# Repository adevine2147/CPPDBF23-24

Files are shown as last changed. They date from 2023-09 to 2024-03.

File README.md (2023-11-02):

# Latest Week Summary (Week 9):
Week # 9     Date: 10/21/23    -    10/27/23

# Aerodynamics Team
### Due milestones:
### Completed milestones: 
### Cost: $0
### Upcoming milestones: 
### Additional Comments:

# Structures Team
### Due milestones: 
### Completed milestones:
### Cost: $0
### Upcoming milestones:
### Additional Comments:

# Payload Team
### Due milestones: 
### Completed milestones:
### Cost: $0
### Upcoming milestones:
### Additional Comments:

# Systems Team
### Due milestones: Finish first draft for Proposal
### Completed milestones: Finishing first draft by Saturday 28
### Cost: $0
### Upcoming milestones: Received feedback and fix proposal on Monday the day before submission.
### Additional Comments:

# Budget
| Subteam | Total | Spendings (This week) | Remaining |
| --- | --- | --- | --- |
| Aerodynamics Team | 800.0 | 0.0 | 800.0 |
| Structures Team (Wed) | 2358.25 | 0.0 | 2358.25 |
| Structures Team (Fri) | 2414.03 | 0.0 | 2414.03 |
| Payload Team | 1000.0 | 0.0 | 1000.0 |
| Systems Team | 200.0 | 0 | 200.0 |

# CPP DBF 23 - 24

This repository is dedicated to efficiently managing Computer-Aided Design (CAD) files, Gantt charts and general file storage for your project.

## Table of Contents

1. [Getting Started](#getting-started)

- [Prerequisites](#prerequisites)

- [Cloning the Repository](#cloning-the-repository)

2. [Uploading](#uploading)

 - [Pushing Changes to GitHub](#pushing-changes-to-github)

 - [Pulling Updates from GitHub](#pulling-updates-from-github)

## Getting Started

  Here's a flowchart
```mermaid
	flowchart TD
A[Terminal go to repo folder on local]-->B[git pull]
B  -->  C[make changes/upload files]

C  -->D[git add .]

C  -->E[git add your-new-file]

D-->  F

E  -->F[git commit -m 'your-commit-messages']

F  -->G[git push]

```

### Prerequisites

Before you begin using this GitHub repository, please ensure that you have the following:

- A GitHub account: If you don't have one yet, you can [sign up here](https://github.com/join).

- Git installed on your local machine. You can download it from [here](https://git-scm.com/downloads).

### Cloning the Repository

To get started, you'll need to clone the repository to your local machine. Open your terminal or Git Bash and use the following command:

```bash

git  clone  https://github.com/adevine2147/CPPDBF23-24.git
```

## Uploading

1.  **Uploading  Files**:

-  To  upload  files  to  your  repository,  click  the  "Add file"  button,  and  then  select  "Upload files"  from  the  dropdown.

-  Drag  and  drop  your  files  into  the  file  upload  area,  or  click  the  "choose your files"  link  to  browse  and  select  files  from  your  local  machine.

-  You  can  add  multiple  files  at  once.

2.  **Commit  Changes**:

-  After  selecting  your  files,  scroll  down  and  provide  a  brief  description  of  the  changes  you're making in the "Commit changes" section.

- Optionally, you can provide a longer description in the "Extended description" field.

3. **Commit New Files**:

- Click the "Commit changes" button to add your files to the repository.

## Pushing Changes to GitHub

1. **Make Local Changes**:

- Before pushing changes, you need to make changes to the files on your local machine. You can edit, add, or delete files as needed.

2. **Stage Changes**:

- In your terminal or Git client, use the following command to stage your changes:

```bash

git add .

```

-  This  command  stages  all  changes  for  commit.

```bash

git add {filename}

```

-  This  command  stages  specific  files  for  commit.

3.  **Commit  Changes**:

-  Commit  your  changes  with  a  descriptive  message  using  this  command:

```bash

git commit -m "Your commit message here"

```

4.  **Push  Changes  to  GitHub**:

-  To  push  your  local  changes  to  the  GitHub  repository,  use  the  following  command:

```bash

git push

```

## Pulling Updates from GitHub

1.  **Fetch  Remote  Changes**:

-  To  update  your  local  repository  with  changes  from  the  remote  repository (GitHub), use the following command:

```bash

git fetch origin

git pull

```

That's it! You've  successfully  learned  how  to  upload  files,  push  changes,  and  pull  updates  in  GitHub!

Latest Week Summary (Week 2):
this is week 2 test

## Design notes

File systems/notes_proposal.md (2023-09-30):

# AIAA Design/Build/Fly Competition - Top Proposals Analysis

## Common Elements:

- **Clear Objectives**: All three proposals have a clear understanding of the competition's objectives and requirements. They emphasize the importance of meeting specific mission goals and scoring criteria.

- **Structured Approach**: Each proposal follows a structured approach, including sections on executive summaries, team organization, conceptual design, manufacturing plans, and test planning. This organization makes it easier for judges to navigate and evaluate the content.

- **Technical Details**: The proposals provide technical details related to aircraft design, including aerodynamics, propulsion, materials, and structural analysis. They show a strong understanding of engineering principles and how they apply to the competition.

- **Sensitivity Analysis**: Sensitivity analysis is used in all three proposals to optimize the design for mission success. This demonstrates a data-driven approach and an understanding of the interplay between design parameters and mission outcomes.

- **Iterative Design**: The proposals emphasize iterative design and testing, indicating a commitment to refining the aircraft's performance through practical experimentation.

- **Team Organization**: Each team has a well-organized structure with designated roles and responsibilities, including faculty advisors. This demonstrates effective teamwork and leadership.

## What They Are Doing Right:

- **Mission Focus**: All proposals prioritize the most critical mission (in this case, Mission 3) based on sensitivity analysis, demonstrating a strategic approach to scoring maximum points.

- **Mathematical Modeling and Simulations**: They make effective use of mathematical modeling and simulations (e.g., MATLAB, CFD) to inform their design decisions and optimize performance.

- **Detailed Manufacturing Plans**: The proposals outline comprehensive manufacturing plans, specifying materials, fabrication techniques, and quality control measures.

- **Testing Strategy**: Each team has a well-thought-out testing strategy that includes both ground and flight tests. This iterative approach helps identify and address design flaws.

- **Financial Planning**: Budgeting and financial planning are included, showing an awareness of the costs associated with participating in the competition.

## What Judges Are Likely Looking For:

When grading these proposals, judges are likely looking for the following key factors:

- **Innovation**: Judges may be interested in innovative design solutions and unique approaches to solving the competition's challenges.

- **Technical Competence**: They expect a strong grasp of engineering principles, as demonstrated through the technical content of the proposals.

- **Mission Optimization**: The ability to optimize the aircraft design to maximize mission-specific scores is likely to be highly valued.

- **Teamwork and Leadership**: Effective team organization, leadership, and collaboration are essential, as they reflect the team's ability to execute their plan.

- **Practicality**: Judges may assess the feasibility and practicality of the proposed design and manufacturing processes.

- **Data-Driven Decision-Making**: The use of data, simulations, and sensitivity analysis to drive design decisions and achieve mission goals is likely to be positively evaluated.

- **Safety and Reliability**: Ensuring the safety and reliability of the aircraft through thorough testing and quality control measures is crucial.

- **Budget Management**: Judges may consider how well the teams have managed their budgets and secured funding for their project.

**Areas for Improvement (Common Across Proposals):**

1.  **Subcomponent Design Schedule:** The proposals lack detailed schedules for subcomponent design. Providing comprehensive schedules for the design and development of individual components could strengthen all three proposals.
    
2.  **Optimization of Ground Mission Weight and Antenna Length:** The proposals could benefit from more detailed information about the teams' approaches to optimizing ground mission weight and antenna length. Offering specific strategies and calculations related to these parameters could enhance the proposals.

3. Ground Mission: The proposal lacks information about the ground mission, including details about the weight to be loaded onto the aircraft. Providing a comprehensive plan for the ground mission would enhance the proposal.

4. Payload Range: The proposed payload range of 1-20 pounds is considered unrealistic. Consider specifying a more reasonable payload range.

5 Optimization and Trade Studies: The methods used for optimization and trade studies could be explained in more detail to provide greater transparency.

6. Design Consistency: Ensure that the proposal maintains consistency between textual descriptions and graphical representations. For example, clarify whether the wing design is rectangular or tapered, and ensure that the number of fasteners aligns with competition rules.

7. Weight, Drag, and Energy Estimation: Include discussions about weight, drag, and mission energy estimation methods. Provide a breakdown of expected empty weight or a goal empty weight.

8. Wind Tunnel Testing: If wind tunnel testing is part of the plan, ensure it is discussed in the proposal, as it appears as a block in the schedule.

9. Testing Plan Detail: Strengthen the description of the testing plan by providing more comprehensive details.

10. Clarify and Correct Discrepancies: Address discrepancies between textual descriptions and visual representations, such as the wing design and fastener counts.

11. Schedule for Prototype Manufacturing: Include a schedule for the manufacturing of the prototype, as it is a crucial aspect of the project.

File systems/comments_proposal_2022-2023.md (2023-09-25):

**Really good proposal overall.** I would like to have seen something on the ground mission - **how much are you planning on loading it to?** Also, a payload range of **1-20 lb is kinda crazy.** Perhaps a smaller volume allotment that could be loaded to a more realistic range. Great work on manufacturing and testing. Those sections are hard at this point in the process, but critical. If you are not thinking about it now, you risk not getting there by the end.

**Good summary and management review.** I think you would have benefitted from explaining your optimization and trade study methods in more detail. Text says you're using a rectangular wing, but picture shows a tapered wing. Discrepancies like this lead to loss of confidence in your explanation. Rules say **2 fasteners to secure antenna, but picture shows 4. Be sure to correct this for your final design.** No discussion of weight, drag, or mission energy estimation methods. Do you have a breakdown of expected empty weight or goal empty weight? How did you optimize box dimensions? The testing plan description is weak. I think you should have devoted more space to that. "**Strongly encouraged to collaborate**" sentence adds no point value, but not talking about wind tunnel testing after showing that as a block in your schedule does reduce your proposal score. Overall, you have what appears to be a good starting point for a successful airplane.

**Team, Overall, well done.** The report was clear and concise. It was obvious that a lot of effort had been expended. The design is well thought out, and shows all areas were considered. **It is important to include a schedule for the manufacturing of the prototype.** All graphics were easy to follow and attractive. Keep up the good work.

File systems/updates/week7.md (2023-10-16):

summary: Week # 7 Date: 10/07/23 - 10/13/23

# Aerodynamics Team

### Due milestones: 
Trade Studies must be done and start XFLR5 practice

### Completed milestones:
A presentation was shared by Andrew for XFLR5 usage and some airfoils were practiced. Some trade studies needed an extra week.

### Cost: $0
(Description of cost, don’t put it in the same line as above)

### Upcoming milestones:
Ansys aircraft simulation will be given to learn and keep XFLR5 practice.

***Additional Comments:***

# Structures Team
 Wednesday 10/11-2023

### Due milestones:
Practice Laminate Wings

Step 1) Move outside with materials to a shaded area
Step 2) Bring two tables
Step 3) Measure:
Part to Vacuum
Vacuum Bag
Gum tape
Peel Fly
Breathing fabric
Step 4) Cut all materials for part
Step 5) In a vacuum bag cut a hole approx. ¼ inch make a cross (X)

Step 6) Stick the vacuum seal
Step 7) Put breathing fabric and peel fly inside the vacuum bag
Step 8) Wear Large gloves and masks cut out carbon fiber to size
Step 9) Wait for resin

### Completed milestones:
Finished practicing laminate wings
 
### Cost: $32.29
(Description of cost, dont put it in the same line as above)

### Upcoming milestones:

***Additional Comments:***

# Payload Team

### Due milestones:

### Completed milestones:

### Cost: $0
(Description of cost, dont put it in the same line as above)

### Upcoming milestones:

***Additional Comments:***

# Systems Team

### Due milestones: 
Start working on Section 4.0

### Completed milestones: 
Section 4.0 waiting for updates for trade studies but the general format already started

### Cost: $0
(Description of cost, dont put it in the same line as above)

### Upcoming milestones: 
Start Gantt Chart for proposal and presentation

***Additional Comments:***

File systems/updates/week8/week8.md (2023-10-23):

summary: Week # 8     Date: 10/14/23    -    10/20/23

# Aerodynamics Team

### Due milestones: 
 Practice XFLR5 and finish trade studies.
### Completed milestones:
Practice was done for XFLR5 and all trade studies were finished. Friday's meeting worked together in XFLR5 for the model and discussed trade studies.
### Cost: $0
### Upcoming milestones: 
### Additional Comments: N/A

# Structures Team
### Due milestones: Assemble and weigh wing for trade study. Finish first practice of wing laminate.
### Completed milestones: Assemble and weigh wing for trade study and wing laminated.
### Cost: $0
### Upcoming milestones: Make a Plan before Aero Data is given.
### Additional Comments: N/A

# Payload Team
### Due milestones: SolidWorks drawing for payload.
### Completed milestones: The First SolidWorks drawing started and dimension analysis is in progress for each mission. 
### Cost: $0
### Upcoming milestones: Mock fuselage dimension shared, keep working on drawing taking into account updated information.
### Additional Comments: N/A

# Systems Team
### Due milestones: Section 4.0 Framework.
### Completed milestones: The section 4.0 framework was done, and in Section 3.0 we started studying trade studies done by the Aero Team. Section 2.0 was started and the first draft was finished.
### Cost: $0
### Upcoming milestones: Correction needed for different sections of the proposal Sections 1.0, 2.0. With help from CE start working on section 3.0.
### Additional Comments: N/A

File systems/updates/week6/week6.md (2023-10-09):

summary: Week # 6     Date: 09/30/23    -    10/06/23

# Aerodynamics Team
### Due milestones: 
Meeting 10/02/2023 Trade matrix updates and progress check-in.
### Completed milestones: 
Most components finished 80% completed Airfoil NACA estimated: 64-ish.
### Cost: $0
### Upcoming milestones: 
Complete trade matrix and share to the Structures team and start CAD. 
***Additional Comments: ***
Got to contact people who did not make it to the meeting and share updates for the structures team.

# Structures Team (Wed)
### Due milestones: 
Learn the program for structures machines for next week's practice for laser and foam cutting.
### Completed milestones: 
 Had the team gather two airfoils: NACA 0012 & NACA 4412 from the NACA Airfoil Website and convert it into a SVG file to be edited in Inkscape. This allowed it to be compatible with the Hotwire Foam Cutter (HWFC) and allowed for the creation of a hole for the wing spar. 
It was then exported as a .DXF file into Vector Tracer which allowed it to create the basic command for the airfoil. Then finally exported as a tap file which was the file type that the HWFC (via MACH 4) would read in order to correctly cut out the airfoil. 
A dry run was first done in order to correctly verify if the HWFC was functioning correctly. The material used for the cutting was a pink insulation foam with 2 in of thickness in order to cut both airfoil shapes with a 2.5 ft span. This was done at 25 PSI.
### Cost: $109.46 
(total cost = [$49.98 * 2] + Tax) ( For the Styrofoam used)
### Upcoming milestones: 
The Wednesday team will study vacuum bagging techniques, resin safety, and handling safety for laminated materials such as: carbon fiber and fiberglass.
***Additional Comments: N/A***

# Structures Team (Fri)
### Due milestones: 
Members are looking to go through the Innovation Idea Labs training, analysis of wing geometry, and begin trade studies.
### Completed milestones: 
Arrival at the Innovation Idea Labs (IIL) in order to use the Laguna Laser CNC to cut out an 18 in Cord airfoil following the NACA 0012 & 4412 patterns. If there is time, then the team will practice putting Mylar (also known as BoPET) on existing wings in the lab.
### Cost: $85.97 
(2'x4'x1/4" plywood sheets 2BC 1Birch)
### Upcoming milestones: 
Make 12 in versions of both airfoils, due next Friday. Possibly also preparing for cutting 3.16 in balsa wood.
***Additional Comments: N/A***

# Payload Team
### Due milestones: 
Updates on payload bay design drafts.

### Completed milestones:
Team getting familiar with Solidworks and beginning a rough design of the dimensions of the payload bay for Structures/Manufacturing.
### Cost: $0
### Upcoming milestones:
Finish payload bay design by Friday (10/13/2023) with a top, side, and frontal view of payload dimensions. Also begin brainstorming a latching method to access the payload.
***Additional Comments: ***
Structures/Manufacturing and Payload are still waiting on Aero for dimensions of the fuselage.

# Systems Team
### Due milestones: 
Finish sections 1.0, 2.0, and 3.0 for the proposal, and start section 4.0.
### Completed milestones: 
Finish section 1.0 and partial of 3.0 for the proposal

### Cost: $0
### Upcoming milestones: 
Finish the Gantt Chart and start updating with Structures for the manufacturing plan on proposal 4.0, section 3.0, and Section 2.0 from the PM by October 11th
***Additional Comments:***

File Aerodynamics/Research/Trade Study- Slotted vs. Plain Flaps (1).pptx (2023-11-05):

## Plain Flaps vs Slotted Flaps

Brandon Henry

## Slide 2

Background

Slotted flaps are an option for the plane, because this design allows high air pressure to flow through the slot, which adds "energy to the wing's boundary layer, delays airflow separation, and produces less drag"

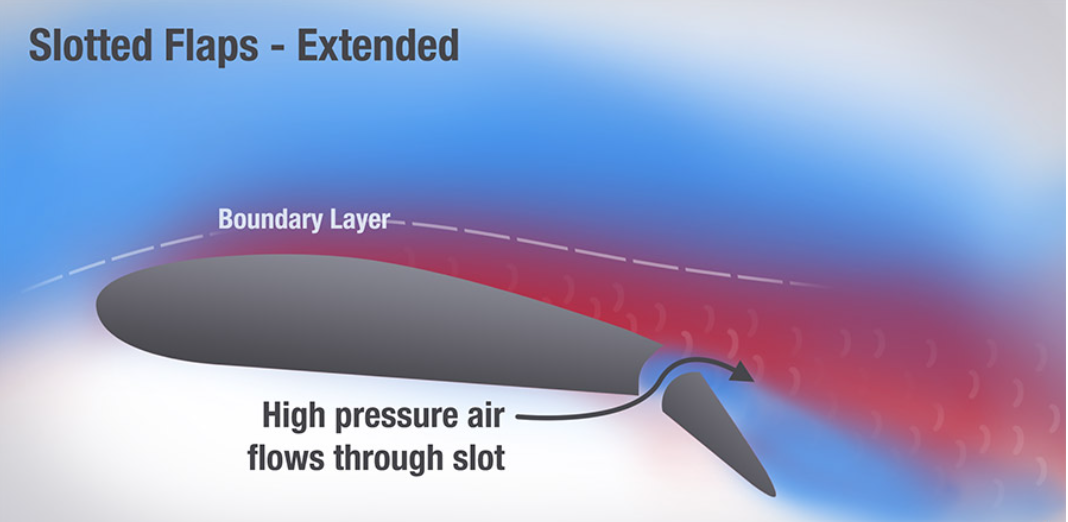
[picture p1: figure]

## Comparisons (Plain vs. Slotted)

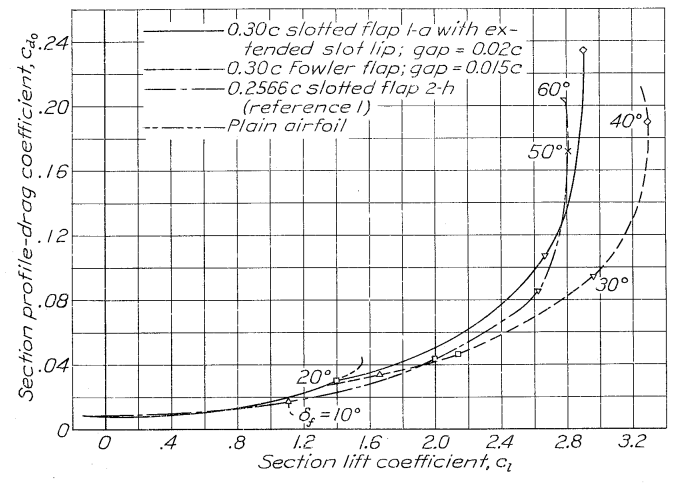
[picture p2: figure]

The Plain Flaps produce a higher drag compared to the slotted flaps at a shallower angle of deflection, while also producing left lift

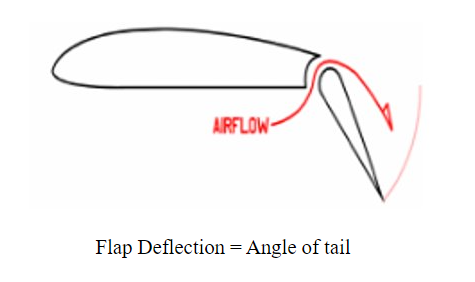
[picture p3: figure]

## Types of Slotted Flaps

Slots can vary based on the spacing between the slots. The difference the between the spacing of the slots is nominal/insignificant. There is another variation of slotted flaps called "Fowler Flaps" which add another slot further down on the airfoil

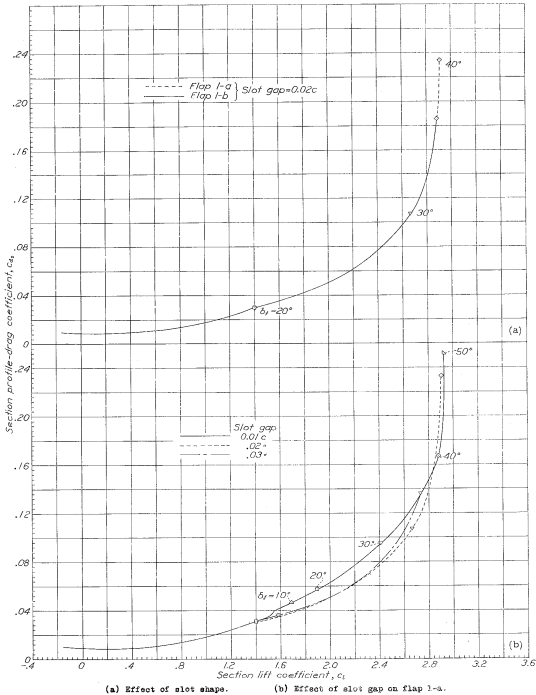
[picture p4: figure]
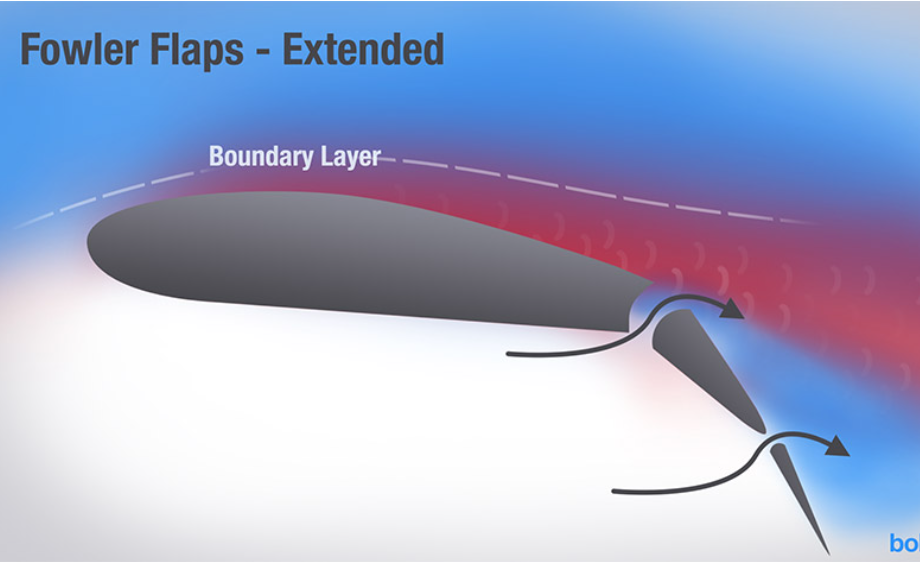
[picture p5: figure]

## Comparisons (Fowler vs. Slotted)

The Fowler Flap produces the most lift with the shallowest Flap deflection

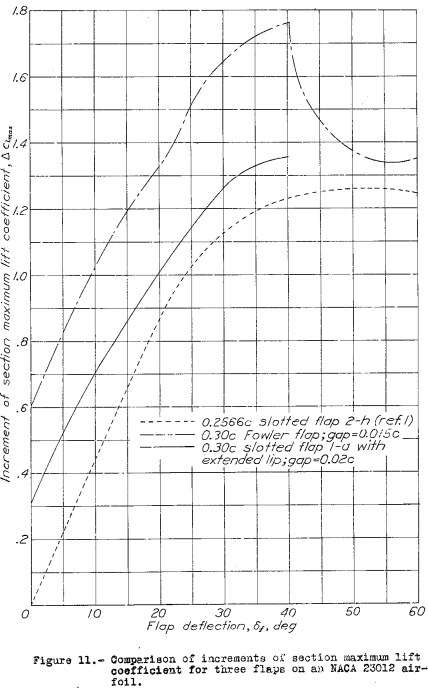
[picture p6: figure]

Flap Deflection = Angle of tail

## Conclusions

In order of best performance we should consider:
  1. Fowler Flaps specifically for its best lift to drag ratio
  2. Slotted Flaps are still a great runner-up option they just don't perform as well as Fowlers
  3. Plain Flap is still a reliable option for flap design, it just will not excel in producing lift compared to the other options

## References

- https://www.boldmethod.com/learn-to-fly/aircraft-systems/how-the-4-types-of-aircraft-flaps-work/
- https://ntrs.nasa.gov/citations/19930085051
- https://www.timetravelair.com/techlibrary/FANASA%20-%20Comparison%20of%20Aerodynamic%20Characteristics%20of%20Double%20Slotted%20and%20Single%20Slotted%20Inverting%2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
- https://www.researchgate.net/publication/347523406_Influence_of_a_slotted_flap_gap_size_on_the_aerodynamic_characteristics_of_a_light_aircraft_wing_at_taking_off_and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

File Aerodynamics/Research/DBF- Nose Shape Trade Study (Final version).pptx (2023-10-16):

## Nose Shape

By: Brandon Henry

## Rounded Noses

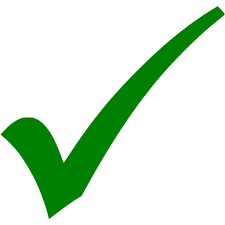
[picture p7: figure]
Green check mark 3 icon - Free green check mark icons

Since we’re worried about lap time, we want the plane to have as little drag as possible. Rounded noses push the air in front of them allowing it to roll over the fuselage with little resistance. In a Subsonic speed setting this is extremely useful (this is why commercial airplanes use this nose model)

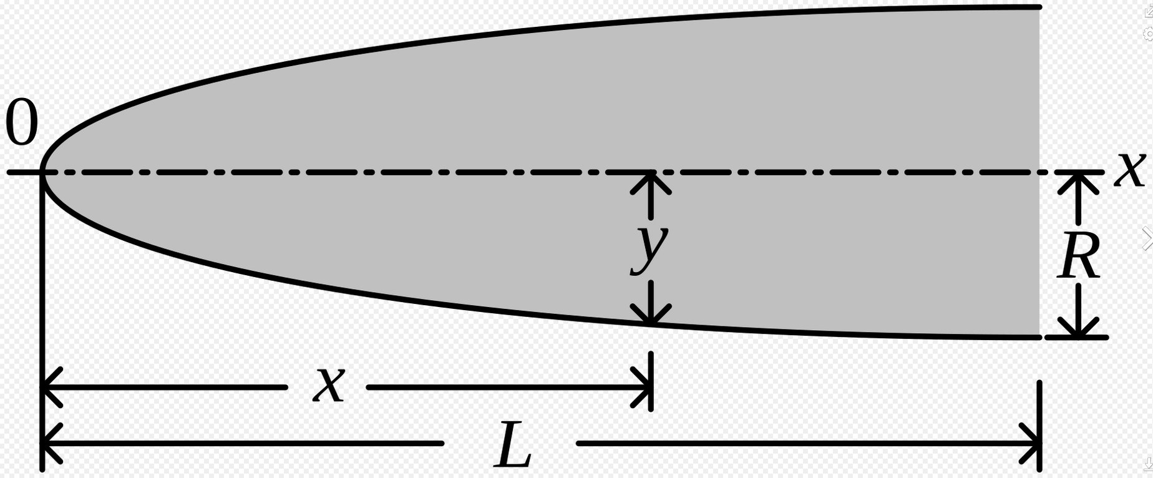
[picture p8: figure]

## Candidate 1 (Cessna Nose)

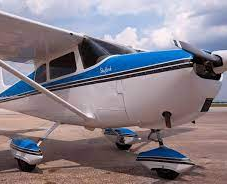
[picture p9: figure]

- Averages 140 mph (120 knots)
- Extremely Blunt nose
- Parasite Drag: 91.2 lbf
- Takeoff Distance: 1,620 feet
- Drag Coefficient: .029

Cessna 172

## Candidate 1

With a nose design like this we have the propeller mounted on the blunt nose itself, which can greatly aid with the thrust of plane, along with aiding in overall stability. One thing we will need to keep in mind is the fact that we need to make sure that our pilot dummy can see out of a window at the front of the plane

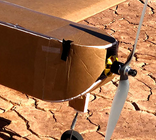
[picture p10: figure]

## Candidate 2 (Boeing 737)

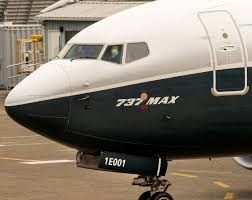
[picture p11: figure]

Boeing 737 Max

- Averages 601 mph (Mach .79)
- Drag Coefficient: .031
- Sharpens at the end of the Nose
- Takeoff Distance: 9,700 ft

## Candidate 2

These blunt noses are modeled more similarly to everyday commercial aircrafts. These shapes are more parabolic and will push more air out of the aircraft's way, as a way of dealing with drag, compared to Candidate 1. This shape will make it easy for manufacturing to make a small window for the plane's pilot to see through

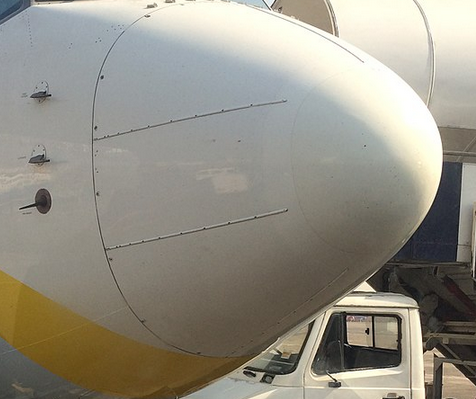
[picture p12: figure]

## Candidate 3 (Airbus A380)

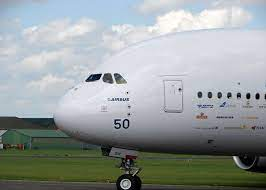
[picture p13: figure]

- Averages 634 mph (Mach .85)
- Parasite Drag: 5,000 lbf
- Take off distance: 9,800 feet
- Drag Coefficient: .368

Airbus A380

## Candidate 3

Similar to Candidate 2 the nose shape will model another commercial aircraft. This shape will make it easy for manufacturing to make a small window for the plane's pilot to see through

## Candidate 4 (Bombardier Global 6000)

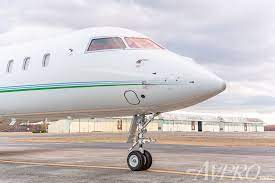
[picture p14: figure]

- Averages 590 mph (Mach .85)
- Takeoff distance: 6,476 feet
- Like Candidate 2, but sharper edge

Airbus A380

## Candidate 4

While on the pointier side of the considered candidates the Global 6000 still performs the same characteristics of the previous candidates, but can also serve as a hybrid between the blunt nose and pointy nose architects

## Summary

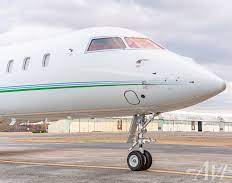
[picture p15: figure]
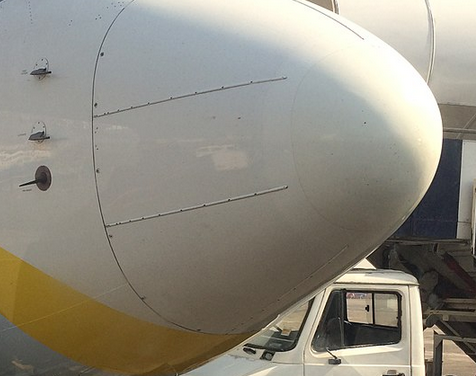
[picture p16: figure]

Each design will need to be slightly modified, so that a window can be made for our dummy pilot.

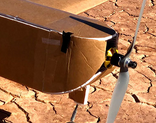
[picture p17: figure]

## Order of Best Options

1. Candidate 1 (Cessna model)-has greatest stability
2. Candidate 3 (A380)- easiest to manufacture
3. Candidate 2 (737)- Decent Drag Coefficient
4. Candidate 4 (Global 6000)- Slimmest design and would require the least amount of material

## Tandem Wings Design

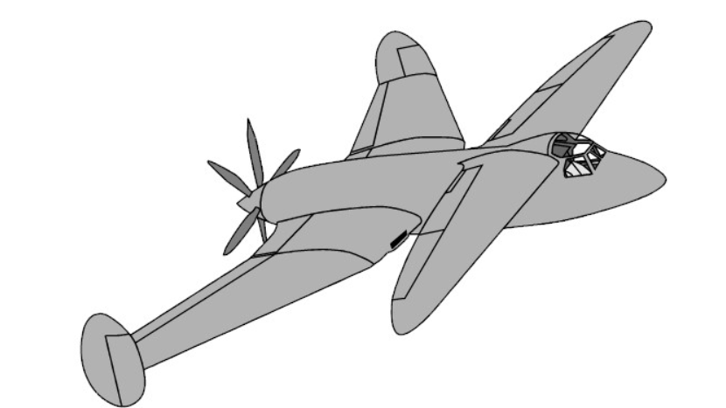
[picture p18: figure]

Tandem Wings provide a high lift while maintaining relatively good stability, due to the increased amount of wing surface area from having two pairs of wings. A potential drawback in this design is the fact that stability is not as stable as other potential designs. Having Tandem wings means that the Plane does not need to have as large of a wingspan. (keep in mind that this design approach require more material overall)

Reference: Design and Optimization of a Tandem Wing Aircraft - KSCST, www.kscst.org.in/spp/45_series/SPP45S/02_Exhibition_Projects/143_45S_BE_4055.pdf. Accessed 5 Oct. 2023.

## Tandem Wing Designs

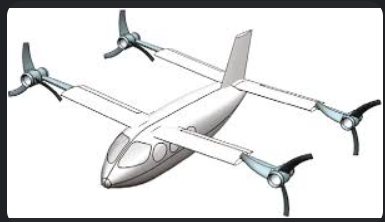
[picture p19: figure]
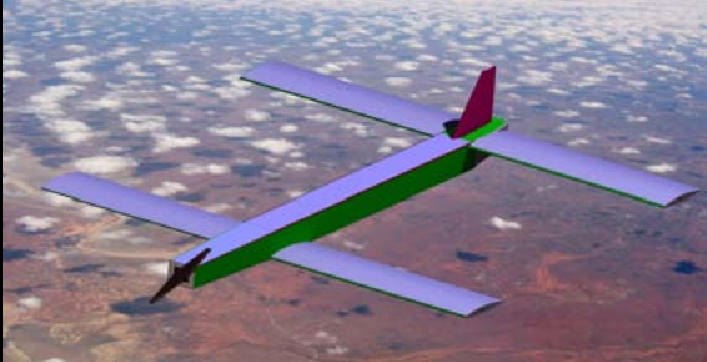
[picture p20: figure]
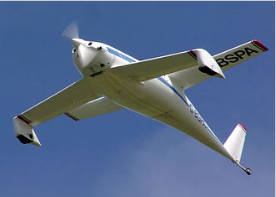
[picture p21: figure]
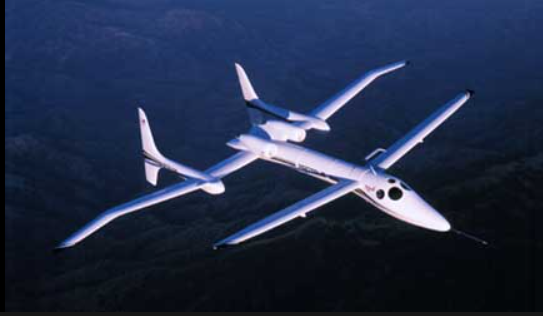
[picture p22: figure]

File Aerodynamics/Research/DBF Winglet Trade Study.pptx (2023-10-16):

## DBF Winglet Trade Study

Created by Het Ghadia

## Pros and Cons of Winglets – Gudmundsson

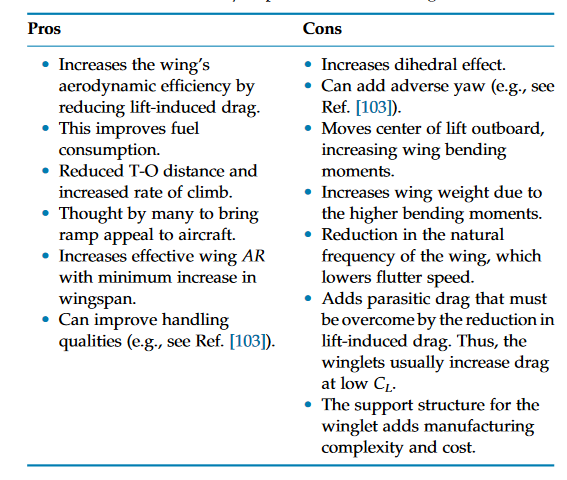
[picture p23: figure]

Ref 103: (https://ntrs.nasa.gov/api/citations/19810003504/downloads/19810003504.pdf)
https://ntrs.nasa.gov/api/citations/19810003504/downloads/19810003504.pdf

## Winglet Designs

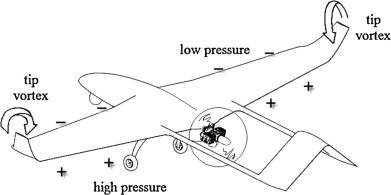
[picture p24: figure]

- Whitcomb Winglet
- Split Winglet
- Blended Winglet

## Whitcomb Winglet


- First-time winglets considered on large aircraft.
- Generates less drag than a wing extension
- May be difficult to manufacture
- Lower winglet is only small to avoid wing strike – does not have to be small


## Split Winglet

- The upper winglet expands the low-pressure region above the wing—the lower expands the high-pressure region below the wing. Thus, it improves the effective AR.


## Blended Winglet -


Difference in drag is marginal compared to Whitcomb Winglet at cruise
Smoother airfoil transition from wing airfoil to winglet airfoil
Reduce pressure peaks compared to Whitcomb Design
Easier to manufacture – 3D Print

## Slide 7


## Conclusion

- Winglet is not needed on this plane
  - It would be an additional weight that may not be worth the reduction on drag
  - And if designed wrong, it would increase drag
- Having said that, a blended winglet should be chosen since it can be easier to manufacture for the plane

## Works Cited

- https://doi.org/10.1016/j.ast.2014.09.006
- https://shareok.org/bitstream/handle/11244/10086/Weierman_okstate_0664M_10946.pdf;jsessionid=BF9FEEA16206F017E796C54CCC6138A0?sequence=1
- Gudmundsson, General Aviation Aircraft Design, Chapter 10 p470-477

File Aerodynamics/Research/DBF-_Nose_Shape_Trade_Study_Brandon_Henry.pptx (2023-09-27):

## Nose Shape

By: Brandon Henry


## Rounded Nose vs. Pointed Nose

Rounded Nose
Attributes:
- Has a higher mass
- Effective in Subsonic settings
- Emulates a parabolic nose shape
- Pushes air in front to allow air to roll over the fuselage

aerodynamics - Why does the bottom part of an aircraft nose curve upwards? - Aviation Stack Exchange

Pointed Nose
Attributes:
- Uses more material to make up the length of the nose
- Effective in Supersonic settings
- Keeps Shockwave away from aircraft
- Conic Shape

Aerospaceweb.org | Ask Us - Rocket Nose Cones and Altitude

## Rounded Noses

Since we’re worried about lap time, we want the plane to have as little drag as possible. Rounded noses push the air in front of them allowing it to roll over the fuselage with little resistance. In Subsonic speed setting this is extremely useful (this is why commercial airplanes use this nose model)

## Pointed Noses

We do want the plane to have as little drag as possible to achieve the best lap time. Pointed noses are most effective at reducing drag in supersonic speed settings, HOWEVER the plane we build is NOT going to be flying at supersonic speeds.

## A Rounded Nose should be used for out Plane

We should try to emulate the nose of a Boeing commercial airplane because it takes into account the need for a small window for a pilot to see through.

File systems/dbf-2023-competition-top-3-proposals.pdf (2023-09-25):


# Texas Tech University

# 2022-2023 AIAA

# Design, Build, Fly Entry Proposal


### Executive Summary

In pursuance of the American Institute of Aeronautics and Astronautics’ (AIAA) 2022-2023 Design Build Fly

competition, this report summarizes the goals of Texas Tech University’s, Raider Aerospace Society’s, Pegasus design

team to develop, analyze, manufacture, and compete with a radio-controlled UAV capable of both transporting a heavy

electronics package payload and mounting jamming antenna/drag inducer adapters at the end of the wings. The aircraft

and all components used in the flight missions must fit within a checked-luggage compliant shipping box with all dimensions

summing to 62 in and weighing no more than 50 lbs. The plane must also be able to takeoff within 60 ft. Design metrics

include the aircraft’s electronic package and jamming antenna capability, out-of-the-box assembly speed, and flight speed.

Through a parameter sensitivity analysis, the optimal design was determined to primarily be maximizing length of

the jamming antenna, minimizing course lap time, and maximizing load on wing structure with secondary goal being

maximizing electronic package weight of the aircraft. To fulfill this objective, a preliminary design has been developed of a

square fuselage with a centrally mounted motor, high-mounted SD 7062 airfoil, T-tail with a tail dragger landing gear, and

modular wingtip adapter for the antenna and drag inducer. A test stand facilitating the ground testing of aircraft weight limits

was also created. A project schedule has been introduced, with the manufacture flow established and the initial prototype

to be started in early November. A maiden test-flight is set to take place mid-January, from which the design will be analyzed,

tested, and optimized for the best competition performance by the fly-off in mid-April.

Figure 1. Organization Structure

### Management Summary

The Raider Aerospace Society (RAS) is the multi-branch

aerospace organization of Texas Tech University. Consisting of

multiple, separate, design teams centered around a unified

management, | RAS | pursues | multiple | aerospace | related

competitions and projects every year. The aeronautics branch,

Pegasus, is competing in the AIAA 2022-2023 Design Build Fly

competition. Pegasus is established in a hierarchical structure in

order to streamline the delegation of tasks and organize the flow

of the design process, shown in Figure 1. A faculty advisor is

available to provide experience and professional insight as well as

advice on official university policy and regulations. The president

of RAS manages the entire organization across its multiple

branches and has executive power on matters regarding Pegasus’

operation. RAS’ officer board consists of the vice president,

treasurer, secretary, and safety officer. The board members work

with the different branches to maintain professional standards of

operation.

2

Shifting into the design divisions, each branch of RAS is headed by a director. The Pegasus director supervises the

general design and progress of the project and works with the design leads to establish suitable goals and timetables.

Additionally, the director facilitates the collaboration and integration of the separate design teams to work towards a final,

complete result, and presents this result back to the officer board in order to source required funding and material. Each of

the three design leads guide their respective design teams in the research and development of the plane: assigning the

distribution of work, monitoring individual members’ progress, and working with other teams to supply deliverables on

schedule. Finally, the design members fill each of the teams based on their preference and develop and test different design

aspects of the project based on the goals for the week.

The three design

teams | are | aeronautics,

structures, and systems. The

aeronautics | design | team

handles the design and

analysis | of | the | airfoil,
empennage, | and | control

surfaces. Analysis includes

the use of XFLR 5, Ansys,

and OpenVSP to simulate

the performance of different

flight surfaces under different

conditions. The structures

team uses Autodesk Inventor


and Ansys to develop and test the fuselage, wing ribbing, ground test fixture and any other structure involved in supporting

the aircraft. Finally, systems manage the electronics, propulsion, and moving mechanisms within the plane.

The general schedule maintained by the director is illustrated by the Gantt chart shown above (Figure 2). The

specific goals for each week are established in biweekly integration meetings, in which the three design teams split or come

together to discuss the project’s progress

and design questions. A summary of the

planned expenses accrued through the

completion of the project is shown in the

budget to the right (Figure 3). Much of the

spending comes from the travelling

expenses, as the manufacture cost of the

aircraft is estimated to be around

$1,793.24. All the equipment necessary

for building the craft (laser cutters, 3D

printers, hand tools, etc.) is accessible

through Texas Tech University and thus

not included in the budget.


Figure 3. Estimated Budget

Figure 2. General Schedule

3

### Conceptual Design Approach

The aircraft will be judged based on a flight performance score determined from the results of four missions. The

objective of each of these missions, the scoring, and the resulting sub-system requirements are presented in Figure 4.

A score sensitivity analysis was; performed to determine the general; design parameters which would be most; beneficial to pursue based on the; competition requirements. The results; can be seen in Figure 5 on the right.; Specific design parameters affecting; M2, and GM were varied while keeping; the other parameters constant. It was; maximize; score; since; the; drastically increases when we minimize; lap speed and increase antenna length.

concluded that M3 should take priority to

GM takes next priority while M2 is the

least impactful. Thus, it was concluded to minimize lap time, and develop efficient counter winglets and maximize wing and

fuselage structure while keeping weight at a minimum.

Mission | Scoring | Objectives | Sub-System Requirements
M1 | = 1 | Fly 1 lap. Demonstrate general airworthiness of design. | Aircraft must be capable of flight.
M2 | = 1 + [ (payload weigℎt ∗ #laps flown)best] (payload weigℎt ∗ #laps flown)n | Fly as many laps as possible within 10 min. Score based on payload weight and laps flown. | Fuselage to hold payload. Securement of payload. Large payload weight and high top-speed will maximize score.
M3 | = 2 + [ antenna lengtℎ mission time )best ] ( mission time )n antenna lengtℎ ( | Fly 3 laps within 5 minutes. Score based on antenna length and mission time. | Antenna to be installed at the end of specified wing and counterweight/winglet to be installed on opposite wing. Securement of antenna. High top-speed and antenna length will maximize score.
Ground Mission | total test weigℎt ( )n max aircraft weigℎt = total test weigℎt ( )best max aircraft weigℎt | Fasten wingtips to ground test fixture and apply test weight to fuselage to test structural integrity of aircraft. | Ground test fixture to fasten to at wing tips. Fuselage and wing structure must be capable of holding test weight. Small max aircraft weight and large test weight will maximize score.

Figure 4. Mission and System Requirement Summary

Figure 5. Sensitivity Analysis

4

Following the design philosophy set by the sensitivity analysis, a shipping box size of 38.5in x 13in x 10.5in was

established to help maximize wingspan and chord length while leaving room for miscellaneous components. The preliminary

wing design is a conventional, high-mounted, square wing design. The layout was selected based on stability, ease of

manufacturing, and analysis simplicity as well as other factors. Once the layout was confirmed, various airfoils were tested

in XFLR 5, and the low Reynolds number SD-7062 was chosen to be the best fit based the anticipated max plane weight of

20 lbs, mission metrics, and trade studies confirming the airfoil has desirable properties. Preliminary sizing of the wings

determined an active surface area of around 4.86 ft²
, which brought the total wingspan of the plane to about 5.8 ft with a

root cord length of 10 in. The flaps and ailerons were designed with a symmetrical airfoil and sized at 15in x 2.5in to provide

effective control surface sizing and desirable maneuverability. The flaps have a maximum deflection of 20 degrees providing

an estimated 28 lbs of lift on takeoff in M2. For simplicity of design, a wing adapter was made to both hold the jamming

antenna and drag inducer depending on flight course direction for M3. The antenna is a PVC pipe varying around 6 in

depending on conditions clamped vertically to the wing through the adapter. Mounted to the opposing wing is the drag

inducer, equalizing the amount of drag felt on both wingtips. The electronics package is a weight filled 3D printed container

of variable weight dimensioned at 7in x 3in x 3in with the fuselage being sized around it. The wings, fuselage ribs, and

weight mounting hardpoints are all supported with four, main, carbon fiber spars that run through the top and base of the

fuselage. For ease of installation and fast assembly time, the nose cone will be removable to install batteries, the electronics

package, and wing servos for all missions. The wing spars are insert into a 3D printed, aluminum reinforced, wing bulkhead

with setscrews to be secured to the main body. The wings will have 2 carbon fiber spars with basswood stringers to minimize

bending stress for GM and wing tip test. The tail boom extends 20 in from the end of the fuselage into a T-tailed empennage

which will be removable for packaging. Liperior 4500mAh 6s batteries were chosen in accordance with the 100 W-h limit for

all mission setups. The propulsion system will consist of a centrally mounted motor at the nose of the wing. According to

the website ecalc, a thrust of 18.95 lbs was achieved using a 17x10 propeller and the Scorpion SII-4025-520KV motor.

Finally, the KST X10 servo will be used to actuate and control the flaps, ailerons, elevator, and rudder. The ground test

fixture is a simple steel tube tower with hinged mounting points to eliminate moment stresses. The proposed aircraft can be

seen in Figure 6.


### Manufacturing Plan


Shown in Figure 7 is the general manufacturing flow for the aircraft. The specific timeline for this flow can be seen

in Figure 2. Once a detailed design of the aircraft has been produced and all the required components exported to their

proper machining files, all raw parts are produced simultaneously across multiple processes. Assembly of the wings and

fuselage ribbing structures along with landing gear and other system components are then created. Finally, the critical

portions of the plane, specifically the wings and fuselage, will undergo a standard Monokote wrap to create an exterior

aerodynamic skin. The outer structures such as the landing gear and empennage are fastened in their respective mounts

and then the wings and fuselage are assembled for testing.

Figure 6. Preliminary Aircraft Design

5

Figure 7. General Manufacturing Flow

To maintain quality during manufacturing, component creation will use a mix of 3D printing, laser cutting, and

general metal working. The fuselage ribs and complex geometry parts are to be 3D printed using several types of plastics

depending on application. Most of the wing ribs and stringers will be fabricated using laser cutters. To assemble the fuselage

and wings, assembly jigs will be created to constrain part alignment. General metal cutting and bending will be used to form

rear landing gear and a portion of the wing mount for ease of attachment when exchanging wings.

### Test Planning

Each of the design teams will be independently managing the testing of sections specific to their focus. This involves

tests to confirm validity of simulated results and analyze performance under un-simulated conditions. Every component of

the aircraft will be fully tested for both operating function and safety as it is manufactured and once assembled into the final

result. General structural and component checks will be performed before every flight, and RAS’ safety officer will also

maintain safe practices during aircraft handling and flight. The separate fields of testing are shown in Figure 8 below:

Category | Test | Purpose | Method
Aerodynamics | Aerodynamic efficiency | Make sure the aircraft design flies stable in flight theoretically before testing a prototype | Use XFLR5 stability tests on aircraft mesh to test wing and tail aerodynamic balance, CL, and CD
| Flight test #1 | Ensure aircraft is stable, controllable, efficient, and able to complete a lap | A prototype aircraft with no payload or antenna adapter will be flown and observed
| Flight test #2 | Ensure aircraft is stable, efficient, and controllable under M2 conditions | Prototype aircraft with maximum payload weight will be flown and observed
| Flight test #3 | Ensure aircraft is stable, efficient, and controllable under M3 conditions | Prototype aircraft with wing adapters, jamming antenna and will be flown and observed
Structure | Structural integrity | Ensure aircraft structures can withstand loadings during flight or ground mission | Use ANSYS (FEA) to apply expected loads
| Wing tip loading test | Confirm wing structure is dependable and strong under high g loads | Lift aircraft at the wing tips to simulate a 2.5g loading/apply loading on tail boom
| Ground mission loading test | Confirm fuselage and wing structure is dependable and strong under high centered loadings | Attach aircraft to ground mission test stand and apply weights to fuselage under CG
Propulsion | Thrust test | Choose efficient motor-propeller combination that provides best thrust-to-weight ratio | Use ecalc to analyze best motor-propeller combination and perform static and dynamic thrust tests with different propellers
Components | Landing gear test | Evaluate strength of the landing gear | Conduct drop tests within marginal heights
Ground | Control surfaces | Ensure all control surfaces are working properly within the design parameters | Ensure plug connections are secure and use transmitter for testing
| CG test | Ensure that CG is within the desired location | Lift aircraft from CL at wing tips to observe if aircraft is level
| Assembly time | Minimize time assembling aircraft | Create as few removable parts as possible. Practice and familiarize with the assembly process

Figure 8. Testing Plans

# National University of Singapore (NUS)

### 2022-2023 AIAA Design/Build/Fly Proposal


National University of Singapore AIAA 2022-23 DBF Competition

### 1.0 Executive Summary

This proposal details AeroNUS’ approach for the design, analysis, manufacturing, and testing processes for the 2023 AIAA Design/Build/Fly Competition.

The objective of this year’s competition is to develop an aircraft capable of conducting Electronic Warfare (EW). This aircraft must successfully complete a staging flight, carry an Electronics Package to simulate a surveillance flight and lastly, carry a Jamming Antenna to simulate a jamming flight. After a thorough analysis of the competition’s rules and scoring system through a sensitivity analysis, the aircraft will be designed and sized to prioritize and maximize Mission 3 (M3) score. Extensive design evaluations and improvements will be conducted for the wings and tail, fuselage, payload, and landing gear before manufacturing prototypes. After working with each component, the plane would be assembled for flight tests. Thereafter, tests for performance are to be held according to Mission 2 (M2) and M3.

The validation of the simulation model design would be done based on the results obtained from test flights. From preliminary review of a training plane, Team AeroNUS chose to go with a flying wing design with a wingspan of 6.43 ft to fit into the shipping box of maximum exterior dimensions of 62 inches. As such, the wing will be split into 4 equal sections of 1.60 ft each. Furthermore, the aircraft must carry an Electronics Package more than or equal to 30% of the total aircraft weight. The Maximum Takeoff Weight (MTOW) will be 14 lb while carrying the Electronics Package of 6.20 lb for M2. For M3, a Jamming Antenna of 1.87 ft will be mounted onto the wingtip of the aircraft, with a counterweight on the opposite wingtip.

### 2.0 Management Summary

2.1 Organization Summary
The 2022/23 AeroNUS team comprises of 10 Seniors, 14 Non-Seniors and 1 Faculty Advisor from the university’s Mechanical Engineering department, who specializes in aerodynamics and propulsion. The team is student-led and has regular consultations with the Faculty Advisor.

2.2 Organizational Chart
The team leaders consist of 1 Chief Engineer and 2 Assistant Chief Engineers, who are responsible for key technical decisions and the overall system integration of the various components in the aircraft. The Administration Manager is responsible for team administration including Treasury, Sponsorships, Procurement, Workshop and Publicity. The Manufacturing Lead heads the fabrication processes and determines the proper build methods. The team is further divided into 5 other sub-teams with their respective leaders, who are responsible for overseeing the team’s progress and deliverables. The Organizational Chart below shows the hierarchal structure of the team.
Team | Roles | Required Skills
Aerodynamics | Airfoil Selection, tail and wing design and dimensions | Knowledge in aircraft performance, stability, CFD and XLFR5 as well as analysis of airfoils and wings
Propulsion & Controls | Decides on propeller, motor, battery, and ESC of aircraft, and control surfaces | Knowledge in propulsion calculations, simulations, and conducting static and dynamic thrust tests
Fuselage | Design of airframe and choosing of materials | Proficient in CAD and FEA software to ensure overall structural integrity of aircraft
Landing Gear | Design and construction of landing gear structure | Proficient in CAD and FEA software
Payload | Selection of payload material and securing mechanism | Knowledge in materials

Table 2.1 – Team Roles and Requirements

Figure 2.1 –
Team
AeroNUS
Organization
Chart


National University of Singapore AIAA 2022-23 DBF Competition

2.3 Schedule/Major Milestone Chart
The Gantt Chart in Figure 2.2 shows our projected schedule and milestones for the competition and tracks the team’s progress. It ensures that ample time is allocated for each milestone for optimal results and that all members of the team are cohesively working together to meet the milestones to complete our best and final aircraft.

2.4 Budget
The team receives funding primarily through the university’s Mechanical Engineering Department, and additional funds are supplemented through corporate sponsorships and crowdfunding. An estimated financial budget of $21,000 covers aircraft manufacturing, airfare, transportation, and lodging, and is summarized in Table 2.2.
Expenses | Item | Estimated Total Cost (USD)
Aircraft Manufacturing | Aircraft Raw Materials (Wood, Foam, Carbon Fiber, Glue) | $950
| Brushless Motor and Propeller | $150
| Batteries | $200
| Electronics and Servos | $200
| Misc. Hardware | $220
Logistics | Transportation | $420
| Airfare (10 pax) | $16,000
| Accommodation (For the duration of the flyoff) | $1600
| Meals | $1260
Total: | | $21,000
Table 2.2 – Projected Expenditure (in USD)

### 3.0 Conceptual Design Approach

3.1 Analysis of Mission Requirements
The objective for this year’s competition is to design, build, and test an aircraft to execute EW missions. There are a total of 4 missions, which consists of 1 ground mission and 3 flight missions. The mission details as well as the sub-system requirements are shown in Table 3.1 below.
Mission | Mission Objective | Payload | Mission Time | Sub-system Requirements
M1: Staging | 3 laps with successful landing | None | 5 minutes | Aerodynamics & propulsion: Ensure aircraft must be able to complete 3 laps within 5 minutes
M2: Surveillance | Fly as many laps as possible with payload added | Electronics Package | 10 minutes | M2 – Fuselage, aerodynamics & propulsion: Aircraft must be able to carry as much payload as possible while not compromising speed to achieve the maximum number of laps M2 – Payload: Electronics Package should take up the highest percentage of total aircraft weight M3 – Payload: Antenna must be securely mounted onto the wing M3 – Aerodynamics: Adverse effects of the Antenna must be accounted for without compromising speed
M3: Jamming | Fly 3 laps as fast as possible with Jamming Antenna attached to 1 wing | Jamming Antenna | 5 minutes
Ground Mission | Test weights are added on top of the aircraft in the heaviest configuration | Configuration Heaviest | 10 minutes | Fuselage: Aircraft must be structurally strong to withstand as much test weights as possible, whilst not increasing maximum weight by too much

Table 3.1 – Summary of Mission and Sub-system requirements

Figure 2.2 –
AeroNUS Gantt Chart


National University of Singapore AIAA 2022-23 DBF Competition

3.2 Sensitivity Analysis
The scoring functions for each mission are shown in Table 3.2 below.
Mission | M1 | M2 | M3 | GM
Scoring Function | 1 for successful flight | (Payload weigℎt × laps)NUS 1 + (Payload weigℎt × laps)Max | Antenna lengtℎ ( mission time ) 2 + NUS ( Antenna lengtℎ mission time ) Max | Total test weigℎt ( ) Max aircraft weigℎt NUS ( Total test weigℎt ) Max aircraft weigℎt Max
Total Score | M1 + M2 + M3 + GM
Table 3.2 – Mission Scoring functions

Based on the sub-system requirements in Table 3.1, as well as the parameters in the scoring functions, the main independent design parameters were identified, namely payload weight in M2, antenna length in M3, as well as total test weight in GM. Mathematical models and relationships between the respective missions’ independent and dependent design parameters were established using formulas, as well as estimates based on the team’s experience. These mathematical relations formed the basis of the sensitivity analysis for the competition and allowed us to investigate the effects of each independent parameter on the dependent parameter and hence identify which one has the most impact on the mission score, as well as the overall score. Based on the respective scoring functions in Table 3.2, Figure 3.1 below compares the overall sensitivity of each mission with respect to the total score. M1 was excluded from this analysis as it does not contribute much to the sensitivity, and we assumed that it was completed successfully.

From Figure 3.1, M3 is the most sensitive mission, followed by M2 and finally GM. As such, our focus will be on maximizing the score in M3 as much as possible whilst not compromising M2 and GM severely. Looking at the parameters in M3 (Figure 3.2), mission time is the more sensitive parameter and is inversely related to M3 score, which is expected given the scoring function. However, since mission time is the dependent parameter, looking at the sensitivity of the antenna length in Figure 3.2, a percentage increase in antenna length would still yield a positive increase in the M3 score since an increase in antenna length outweighs the increase in mission time. As such, antenna length would be maximized to maximize M3 score. However, it must be noted that missions M2, M3 and GM are interrelated. In this case, the payload weight and wing dimensions sized in M2 will have a direct effect on M3 and GM, and may be in direct conflict with each other. As such, the sizing of the aircraft should not be done independently for each mission. Since M2 is most likely the heaviest flight mission, it was sized first followed by M3 and GM and the optimal configuration was selected for our preliminary design.

3.3 Preliminary Design
Based on the mathematical relations and the sensitivity analysis, the team developed a MATLAB algorithm, AeroSim2023, that computes the optimal aircraft configuration that maximizes our total score. Independent variables of wing aspect ratio (AR), wing area (S), motor power, total aircraft mass and antenna length are iterated in AeroSim2023 to obtain the optimal dimensions, whilst bounded by the maximum exterior box dimensions of 62 linear inches. A preliminary sizing was done for M2 which showed that M2 favors a large S to allow for a heavier payload weight, as well as a large AR to increase Vmax. However, M3 and GM do not favor a large AR since the adverse yawing and rolling effects of the antenna, caused by vortex shedding, in M3 will be increased, as well as the wing structural bending moment in GM. As such, wing AR must be reduced to restrict wingspan. Given this and the overall box constraint, a mathematical function was created and implemented to
Figure 3.1 – Overall Mission & Parameter Sensitivity | Figure 3.2 – M3 Parameter Sensitivity

Figure 3.3 – Optimal Sizing Graph
Figure 3.5 – Arrangement of Fishing Weights Inside Electronic Package; Figure 3.6 – Antenna Adaptor

National University of Singapore AIAA 2022-23 DBF Competition find the optimal balance between the number of wing sections and AR that fits within the box to maximize S. Figure 3.3 shows the results from AeroSim2023. The results showed that the wing should be broken into 4 sections, with 2 sections for each left and right wing and will have an AR of 4, S of 10.33 ft² ,
and a MTOW of 14 lb. This gives a wing loading of 1.36 lb/ft²
. From here, a
flying wing, without any sweep or taper, was concluded to be the best option given the limited box space. The aircraft will adopt a high wing configuration, utilizing a reflex airfoil to achieve longitudinal stability. The MH70 airfoil was chosen as it has a high CLmax

of 1.3 and a corresponding Vstall of 29.60 ft/s for M2. This means a lower takeoff speed and lesser time spent on the ground. Vmax was calculated to be 133.76 ft/s. The wing will adopt a polyhedral configuration, with a dihedral angle of 15⁰ on the outboard wing section for roll stability. A vertical tail fin, mounted on a carbon fiber boom, will be attached to the rear of the fuselage for directional stability and to dampen the adverse yawing moments of the antenna in M3. Elevons will be used for pitch and roll control. The conceptual design of our first prototype is shown in Figure 3.4 and detailed values and specifications are given in Table 3.3 below.

For M2, an Electronics Package of 3” x 3” x 6” will be filled with lead fishing weights to achieve the desired weight of
6.20 lb as shown in Figure 3.5. For M3,
since maximizing antenna length will
maximize mission score, it will take the longest length of our shipping box (1.87 ft) and will be secured using a 3D-Printed attachment shown in Figure 3.6, which will be mounted to the wingtips. To balance the antenna’s weight, a counterweight will be attached onto the opposite wing.

The propulsion system will adopt a tractor configuration. With a power loading of 113.40 W/lb and taking into consideration the 100 Wh battery limit, a 6S, 4500 mAh battery was chosen. While this only gives us a flight time of 3.34 mins for M2, it still gives us a higher score compared to flying the entire 10 mins and scaling down the size of the aircraft, which means a lighter payload. The aircraft will be powered by a SunnySky X Series V3 X4120 480kV Brushless Motor, paired with a 16 x 8-inch propeller. The fuselage will be as small as possible to just accommodate the payload and propulsion system, which will be positioned accordingly to give us a static margin of between 5-10% for the flight missions. A tail dragger landing gear configuration will be adopted as it is light and has less drag.

MTOW | 14 lb | Propulsion | Wing | Tail
Dry Weight (including propulsion) | 7.80 lb | Configuration | Tractor | Wing Area | 10.33 ft² | Tail Type | Vertical Fin
Shipping Box | | Propeller Size | 16 x 8 inch | Aspect Ratio | 4 | Tail Area | 1.22 ft²
L x W x H | 1.62 x 1.87 x 1.62 ft | Power Loading | 113.40 W/lb | Wingspan | 6.43 ft | Tail Boom Length | 1.57 ft
Weight | 8 lb
Fuselage & Payload | | Motor Power | 1793.76 W | Chord Length | 1.60 ft | Vertical Tail Volume Coefficient | 0.036
Electronic Package Mass | 6.20 lb | Battery Capacity | 4500 mAh | Wing Loading | 1.25 lb/ft² | Landing Gear
Antenna Length | 1.87 ft | Propulsion Mass | 2.63 lb | Airfoil | MH70 | Configuration | Tail Dragger

Table 3.3 – Aircraft Specifications

### 4.0 Manufacturing Plan

4.1 Preliminary Manufacturing Flow
Figure 4.1 below illustrates our team’s proposed manufacturing plan, which includes three intermediate prototypes before fabrication of our final aircraft. MATLAB and XFLR5 simulations will be used for preliminary sizing of aircraft specifications.

Figure 3.4 – Prototype Design


National University of Singapore AIAA 2022-23 DBF Competition

The aircraft will then be designed and modelled using CAD software, with its aerodynamic and structural performance validated using CFD and FEA respectively. A thrust stand will be used to select the most efficient propeller for our flight requirements. Preliminary research and wind tunnel tests will also be conducted to analyze the effects of the antenna mounted on the wingtip in M3, such as the Von Karman vortex street.

Figure 4.1 – Manufacturing Plan

4.2 Critical Manufacturing Process
After initial analysis done using SOLIDWORKS’ structural simulation program, we determined wood to be the primary material for our aircraft structures, namely balsa, basswood, and plywood, which have suitable mass and yield strengths. The use of composite materials (carbon-fiber rods) will also be considered for flight-critical components such as the wings, fuselage, and tail boom (M2 and M3). This ensures optimal strength-to-weight ratio of our aircraft, allowing it to withstand maximum loads during the missions all while being lightweight (M2 and GM). To ensure that wooden components are consistently fabricated to precise specifications, they will be cut to size using a CNC laser cutter. For hand-cut parts, the use of custom-made jigs will be employed to minimize human error during fabrication. Additive manufacturing will also be used to achieve complex geometry in components like the antenna attachment used in M3. Both the wings and vertical tail will be manufactured using the rib-and-spar method, which provides the best strength-to-weight ratio. Upon completion of the manufacturing phase, propulsion systems and avionics will be fully integrated into the aircraft. Finally, all exposed surfaces will be skinned using Monokote film which improves airframe strength while adding very little weight.

### 5.0 Test Planning

After assembly of each prototype, we will conduct 3 types of tests for validation against their simulated counterparts, as well as to ascertain their safety and reliability during operation. These include preliminary design tests on the propulsion systems, as well as ground and flight tests on the fully assembled prototypes. The first prototype will be used to determine flight characteristics, trim conditions, and the capabilities of our aircraft in carrying the required payloads for M2 and M3 (≥30% of plane’s gross weight and antenna mounted on the wingtip respectively), as well as the effects of the antenna on our flight performance. Test weights will be added to ascertain the actual structural margin for the prototypes for GM. The second and third prototypes will be designed to be more efficient and reliable based on data gathered during testing, which will in turn provide further insights to be fed back into the final design of our aircraft. Battery sizes will also be fine-tuned along the way based on actual consumption during the tests to optimize for flight time and performance. These will all culminate in a competition-ready plane of peak performance, which yields the maximum possible score during the competition.

Figure 5.1 – Testing Plan


1

## 2022/2023 AIAA Design/Build/Fly Proposal


### 1 Executive Summary

This proposal provides detailed concept design, plans for further design, testing and team management of the University

of Maribor’s team of the 2022/2023 AIAAA Design, Build, Fly Competition. The team’s main objective for the 2022 DBF competition

is to design and build an aircraft for the most efficient execution of electronic warfare. The aircraft should be capable of flying with

approximately 7 lbs payload and carry a 40” surveillance antenna, mounted to one of the wing tips. The maximum speed in level

flight should be about 80 KTAS and the best glide speed, at which the endurance mission will be flown should be around 50 KTAS.

The structure should be capable of withstanding the load of no less than 100 lbs and the whole aircraft should fit in the box with the

constrained dimensions. This is the fifth DBF competition in which the ADUM team is going to participate, therefore taking into

account previous experiences and gained knowledge, the expectations and goals this year are higher. The team’s budget is $3.500

for materials needed and $18.150 for transport and accommodation. This year’s main challenges are limited battery energy storage,

the size of the shipping box, the requirement for multiple wings and a strong antenna attachment. Considering different

configurations, a high wing monoplane with a single motor in the front and a conventional tricycle landing gear, has been decided.

A single lithium battery pack (LiPo) will be used for the propulsion due to its superior performance per unit mass. This year there is

an enhancement of the manufacturing procedures planned, by including additive manufacturing and reinforcing the parts with fiber

technology. This way, complex-shaped parts can be manufactured, with superior aerodynamic efficiency and improved rigidity per

unit mass. To prepare for the flying missions, the team has conducted a multi-objective optimization using an individually developed

Python algorithm. This way, optimal combination of the design parameters for maximizing the total score of all flying missions, has

been obtained. An intensive ground and flight testing is planned to further improve the total score and to ensure the early discovery

of significant improvement potential and sufficient reliability of all systems.

### 2 Management Summary

### 2.1 Description of Organization

The 2022/2023 University of Maribor team (ADUM) consists of one faculty advisor, 7 bachelor students and 4 graduate

students and one non-student pilot. Our project leader oversees the project with occasional consultations with the faculty advisor.

The project is solely student-led. With this year’s growth of members, we departmentalized our team with our senior students leading

each department to ensure all regulatory rules are met. Departmentalizing enables our project leader to monitor each department’s

progress and design review. In addition, it offers better cooperation between each workstation. Our team holds weekly meetings for

Project manager

Mitja Štrakl Pilot

Jernej Jurhar

Faculty advisor

Dr. Janez Kramberger
Chief Engineer

Peter Orešnik

Aerodynamics

Ana Gregor
Jaka Perne

Structure

Eva Gradišnik

Manufacturing

Jure Stošić

CAD

Gregor Popič

Elec. & Propulsion

Blaž Morel
Martin Rolih

Documentation

Nina Horvat
Tjaša Malis

Figure 1: Organizational chart

2

task allocation and discussion, concerning workflow, major decisions and satisfactory progression according to our schedule. Each

department has its own leader, who is responsible for communicating and updating our project leader about the completion of each

task and ensuring a safe work environment in each workstation, with emphasis on the quality of their work. Our pilot was chosen,

according to his background in flight aviation and simulation training. Figure 1 shows team’s structure. For each department there

are specific skills and responsibilities required for every member. Not to be cast aside, leadership of our team also holds

responsibilities. Figure 3 shows responsibilities of our teams’ leadership. Shown below are the leadership position’s duties and skills

required. All team members are included in various aircraft manufacturing processes in order to complete the aircraft as quickly as

possible.

Table 1: Department sub-teams responsibilities and skillsets
Department | Responsibilities | Required Skillset
Aerodynamics | Shaping, sizing aerodynamic bodies and surfaces. Aerodynamic analysis to ensure efficiency, stability and aircraft control. | Knowledge of aerodynamics, stability and control. Proficiency in aerodynamic simulation & analysis software.
Structure | Airframe construction, selection of materials and manufacturing procedures. Structural analyses and A/C component testing. | Proficiency of non-destructive testing methods. Knowledge of metallurgy. Knowledge in statics and stress calculation.
Electronics & Propulsion | Design of radio control, transmitter signaling. Connectivity of onboard controls. Propulsion sizing and performance analysis. | Knowledge of signaling and harmonic oscillations. Knowledge of electronics, wiring skill. Knowledge of propulsion systems.
Computer-Aided Design | Design of molds, wing, tail, landing gear, etc. | Proficiency in Computer-Aided Design and structural analysis software.
Manufacturing | Electrical powering, wiring, telemetry for data logging. Creation of molds, wing, tail, landing gear, etc. | Knowledge of different material properties. Knowledge of electronics, engineering. Manufacturing skill and processing of different materials.
Documentation | Handling of general administrative work, sponsorships, budgeting and other documentation. Assistance to other teammates in manufacturing of the aircraft. | Proficiency in secretary work and organizational skill. Proficiency in publishing on media networks, video end photo editing software.
Project Lead / Chief Engineer | Allocation of tasks, managing meetings, determining workflow. Management of departments, overseeing quality of work | Proficiency in management and team lead. Organizational and planning skills. Quality management and control experience.

### 2.2 Budget

The size of the aircraft has a big influence on the total cost of the project. Expenses for the materials and manufacturing of

the aircraft were estimated using previous seasons’ expense figures and results of a design parameters study. All funds for materials

and components are procured from local sponsors. The team’s confirmed 2023 DBF budget is $3.500, and it is to be used for

materials and components. The team’s focus is on effective use and redistribution of the budget. Additional machining costs will be

covered by the University of Maribor. Transportation, accommodation and allowance costs are based on trip offers from a local

travel agency and will be covered by the State Student Fund, which grants $1.190 (1,200€) per participant. The total estimated

costs for manufacturing materials, electronics and travel and accommodation for the team are shown in Table 2.

Table 2: Estimated budget:
Manufacturing materials | Number | Cost [1 pc] | Cost | Electronics | Number | Cost [1 pc] | Cost
Balsa | 5 | $ | 12,00 | $ | 60,00 | Electric motor | 2 | $ | 150,00 | $ | 300,00
Plywood sheet | ESC | 2 | $ | 200,00 | $ | 400,00
Styrofoam | 20 | $ | 10,00 | $ | 200,00 | Transmitter | 1 | $ | 200,00 | $ | 200,00 XPS Foam sheet | Receiver
3D-printing ABS Filament | 4 | $ | 30,00 | $ | 120,00 | Main battery pack | 10 | $ | 30,00 | $ | 300,00
Carbon fiber rod | 5 | $ | 65,00 | $ | 325,00 | Servomotor | 20 | $ | 4,00 | $ | 80,00
MonoKote roll | 3 | $ | 40,00 | $ | 120,00 | TOTAL | $ | 1.280,00
Fiberglass | $ | 300,00 Resin | Travel and Accommodation | Cost [1 pc] | Cost

Adhesives
| | | | $ | 60,00
Flight tickets (12 persons) | $ | 700,00 | $ | 8.400,00
Bolts | Rent a car (10 days) | $ | 120,00 | $ | 1.200,00
Nuts | Fuel (10 days) | $ | 500,00
TOTAL | $ | 1.185,00 | Lodging (10 days) | $ | 5.000,00
Meals (12 persons, 10 days) | $ 1.000,00
TOTAL | $ 16.100,00

### 2.3 Major Milestone Chart

After the release of the competition rules, a Gantt chart (Fig. 2) was made, to set project deadlines to ensure the desired

progress. The progress is recorded in the chart, and it will be presented thoroughly in the Design Report.

3

### 3 Conceptual Design Approach

### 3.1 Mission requirements

The objective for this year is to design and build an aircraft to carry a heavy payload and an externally mounted antenna.

Considering those objects, initial sub-system requirements are defined, which serve as basic guidelines for the aircraft configuration

selection and the preliminary design.

Table 3: Mission objectives, score and subsystem requirements
Mission | Payload | Mission objective | Time | Score | Sub-system requirements
M1 | None | Complete 3 laps | 5 min | M1 = 1 | • Demonstrated robustness and reliability
M2 | Electronic package | Maximize laps flown in time window | 10 min | M2 (Wp ⋅ NLAPS) = 1 + (Wp ⋅ NLAPS) MAX | • Minimize drag at the mission cruise speed • Maximize structural resistance at given empty weight, additionally reinforce the payload carrier • Maximize lift at T/O speed, to ensure take-off in less
M3 | | Minimize time required tR for 3 laps | 5 min | (LA/tR) M3 = 2 + | than 60 ft Antenna
(LA/tR

)MAX

GM | Max Payload (AUW)

Apply test weights up to
maximal load WTEST

10
min

GM

=

(WTEST/AUW)

(WTEST/AUW)MAX

- Maximize wing load resistance
- Ensure even load distribution, to reduce stress on the wing tips

### 3.2 Score analysis and sensitivity

The overall flight mission score consists of four individual mission scores, three

of which are the subject of the present optimization problem. Those are Mission 2 (M2),

Mission 3 (M3) and Ground Mission (GM). After analyzing each missions requirements,

two significant design parameters were identified – payload weight Wp and antenna length

Figure 3: Individual mission score sensitivity

LA. Payload weight predominantely affects the expected performance in missions M2 and

GM, with an inverse effect between the two as indicated in Fig. 3. For M2, increasing the

Wp increases the mission score, suggesting that the aerodynamic penaly of the increased

AUW is outperformed by the benefit of the increased Wp. Based on the preliminary aricraft

sizing and aerodynamic analysis, it was established that increasing the Wp can even have

a favourable effect on the aerodynamic performance as it increases the best glide speed.

The extent of the Wp increase is however limited by the energy available in the battery, as

W1 | W2 | W3 | W4 | W1 | W2 | W3 | W4 | W1 | W2 | W3 | W4 | W1 | W2 | W3 | W4 | W1 | W2 | W3 | W4 | W1 | W2 | W3 | W4 | W1 | W2 | W3 | W4 | W1 | W2 | W3 | W4
ADUM, DBF 2023 | Sep-22 | Oct-22 | Nov-22 | Dec-22 | Jan-23 | Feb-23 | Mar-23 | Apr-23

Aircraft design
Publication of rules

Sub-tasks
| | Actual timing
| ✈ | | Important dates
| | | | | Planned tasks
Reviewing draft rules
Sensitivity Analysis
Concept design
Preliminary Design
Detailed Design
Design Review & Modification Manufacturnig
Prototype 1
Prototype 2
Prototype 3
Final model
Analysis and simulations
Aerodynamics
Structure
Propulsion
Components
Testing
Ground Test 1
Ground Test 2
Ground Test 3
Ground Test 4
Important Dates
Proposal
Proposal due | | ✈
Design report | 31-Oct
Design report due | | | | ✈ | | 13.-16. Apr
Content Fly-off | | | 25-Feb | | | | ✈
Figure 2: Project plan Gantt chart, with milestones

4


the power required to sustain flight at such conditions should not lead to premature

battery drain. As far as the GM is concerned, increasing the Wp (and with that the AUW)

reduces the mission score, asumming that the design structural load margin is kept the

same. Nevertheless, it has been demonstrated that the benefit in M2 due to increased

Wp outweighs the penalty in GM, meaning that the Wp should be optimized for M2. In

mission M3, the objective for optimization is the antenna length LA. Preliminary drag

calculations show that the maximum structural cruising speed VNO is decreasing with the

factor 1/LA, due to bending moment acting on the antenna. The score in M3 is a tradeoff

between LA and mission time. Additionally, with increasing LA, a linear speed penalty

has been added to VNO, due to the stability concerns. An optimization problem-

maximizing the overall score, has been peformed (Fig 4), which estimates the optimal

Wp of around 60% AUW and the optimal LA of around 85% LA,max.

### 3.3 Preliminary design

Concluded from the sensitivity analysis, a low drag, high

structural resistance and a positive static and dynamic stability are the

key design objects. As a result, a high-wing monoplane with tricycle

landing gear configuration is selected (Fig. 5), as a trade-off between

drag, structural resistance and ease of manufacturing. The initial wing

design proposes a tapered wing with 5.3ft span, surface area of 4.3 sqft

and an aspect ratio of 6. Basic design is proposing CLARK-Y airfoil, due

to its favorable lift/drag relationship, while a further optimization via the

CFD tools is pending. Due to the box size limitation, a bi-section

fuselage with length of 4 ft is proposed, with empennage integrated into

its rear section. Empennage dimensions and moment arms are

optimized within the distance constraining to ensure positive static and

dynamic stability, resulting in the horizontal tail-plane span of 1.5ft and

height of the vertical tail-plane of 1 ft. Given the gross airplane size, a

single front mounted electric-motor propulsion is selected with

maximum power of 2kW. The energy requirements of the propulsion

system are supported by the 6S 4500mAh lithium (LiPo) battery, which

Figure 5: Preliminary aircraft model

falls just under the 100 Wh energy storage limit. For the structure and propulsion of the presented aircraft, the predicted basic empty

weight is 5.95 lbs. To allow for at least 7lbs payload, the design MTOW is 14 lbs (with small margin for an additional load). According

to the preliminary drag and lift calculations, such a configuration results in stall speed of 33 KTAS, best glide speed of 50 KTAS and

a maximum level-flight speed of 80 KTAS. Payload carrier is positioned approximately at the CG point, so that a flight configuration

with or without payload can reach the design CG envelope, which is at 32-36% MAC according to preliminary calculations. Antenna

mount is integrated in each winglet, which is bolted onto the wing. Threaded inserts in the wing are reinforced all the way to the

main spar, to enable the ground test fixture to be attached to the same structure, thus reducing the mass of installing additional

mounts.

Figure 4: Optimized total score

• Aircraft concept • Initial design; • Materials selection • Standard parts; • Manufacturing • Prototype assembly; • Analysis & simulation • Aerodynamics (CFD) • Structural (FEM); • Testing • Ground tests • Flight tests; • Final aircraft; • CAD Design • Components • Mechanisms; • Feedback • Failure analysis • Updated design; Figure 6: Manufacturing flowchart

5

### 4 Manufacturing plan

Manufacturing flowchart is illustrated in Fig. 6 and consists of several design and analyses stages, manufacturing and

testing. This is an iterative process, where test results are evaluated, failures analyzed and improvement potentials defined. They

are then returned back into the design loop trough the feedback stage, where design is updated accordingly and the process then

repeats. As determined in the preliminary design guidelines, this year the manufacturing will be enhanced employing the additive

manufacturing technologies (3D print). This will mainly be applied for front fuselage sections. As the technology allows for producing

complex-shaped parts, the aerodynamic efficiency (low drag) objective will be prioritized in the fuselage design. Rear fuselage

section is produced from a carbon tube at the end of which an empennage is mounted. Front and rear fuselage sections are

assembled by the compressible joint and integrated in the front fuselage section. Critical components will be reinforced with carbon

fibers, to ensure that structural resistance requirements are met. The main wing halves employ a sandwich construction with a foam

core and carbon fiber shell. Carbon tube will be used as a main wing spar and to connect the two halves and the fuselage.

### 5 Test plan

The test plan schedule is given in Table 4 and proposes two main phases, namely ground testing and flight testing. The

ground tests will start early in the design phase, to identify faults as soon as possible and reduce time and design efforts, required

for their mitigation. Static and dynamic thrust and energy consumption will be measured including stress testing of the electrical

components, to ensure their durability and reliability. Wing load testing will be performed thorough the design, to improve load

resistance to the greatest extent. Fuselage sections will also be stress tested, to ensure that the deformations are within tolerance

for conducting all flight missions. Flight testing, which will take place at an airport in Murska Sobota, will begin after the first prototype

is built. First set of flights will determine aircraft’s performance, stability and airframe capabilities. Second set of flights will determine

the take-off distance, stall speed, best glide speed, and maximum level flight speed dependency on the TOW. Third set of flights

will determine the propulsion characteristics in flight, i.e. energy consumption at different cruising speeds. After that, the endurance

will be analyzed using different payload weights and throttle settings, to optimize the throttle management for the endurance flight.

Table 4: Test plan
Phase | GT1 | Test Static thrust | Objective Measure thrust, current and voltage specifications throughout the throttle curve and for different propellers | Deadline Ground tests 4.Nov
| GT2 | Dynamic thrust | Install the thrust test bench on the vehicle. Measure thrust, current and voltage specifications throughout the throttle curve at different speeds. | 18.Nov
| GT3 | Wing load resistance | Mount the wings at the tips. Install the test weights until structure damage. Analyze the damage, improve the structure. | 2.Dec
| GT4 | Landing gear | Install the gear on the fuselage. Apply weight up to MTOW. Drop the fuselage from 2 ft. | 16.Dec
| FT1 | First flight test | Perform a normal take off, climb, traffic pattern, land. Debrief, analyze static stability. | 30.Dec
| FT2 | Performance and stability flight | Gain altitude, perform stability testing: Longitudinal stability: Pitch moments, 3211 maneuvers. Lateral stability: Steady sideslip. Lateral stability: Rudder response. | 13.Jan
| FT3 | Take off performance, Speed tests | Perform multiple flights at various TOW. Measure TO distance, stall speed, best glide speed, max speed. | 27.Jan
| FT4 | Cruise performance | Perform multiple flights at various TOW. Measure speed and energy consumption characteristics. | 10. Feb
| FT5 | Endurance test | Using the results from FT4 and FT5 select optimal TOW. Perform 10 min endurance flight, optimize throttle management. | 21. Feb

Flight tests

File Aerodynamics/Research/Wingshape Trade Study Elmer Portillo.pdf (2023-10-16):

# Wingshape Trade Study AIAA DFB 2023-2024


# Elmer Portillo


# Factors to consider

1. Lift Coefficient
2. Drag Coefficient
3. mass
4. stability
5. Manufacturability & Feasibility
6. Overall Aerodynamic efficiency

Candidates | ● Rectangular (Constant Chord)
| ● Trapezoidal (Tapered )
Explanation: Considering our specific | ● Elliptical
constraints, which include but are not limited to
the need for high lift at low speeds, efficient lift
distribution, enhanced stability, manufacturability
and feasibility these three configurations represent the optimal candidates.


# Rectangular (constant chord)

Pros:
1. Feasibility - Easy to design, build and maintain.
2. High Lift - advantageous for STOL operations
3. Low Stall Speed - Aircraft can maintain controlled flight at lower speeds
4. Predictable handle and control - could be advantageous for faster lap times.


Cons:
1. Less efficient than tapered and elliptical wings
2. Lower maneuverability due to square tips

# Rectangular Wing - Slight Tip

adding wingtips to a rectangular wing can be a valuable modification to enhance the wing's performance and characteristics.

1. In addendum with previous slide:
a. Reduced Induced Drag
b. Increase lift
c. Enhances control
d. Reduces wingtip Vortices
e. Improved Stability and Safety


# Trapezoidal (Tapered)


Cons:
1. More difficult to construct than rectangular
2. Higher stall speeds than rectangular wing

Pros:
1. More aerodynamically efficient than rectangular wings leading to better speed and efficiency.
2. Improved glide ratio
3. Maneuverability - allow for tighter turns and more dynamic flight capabilities.

# Elliptical


Cons:
1. Difficult to construct, more difficult than rectangular and tapered wing
2. Higher stall speeds
3. Reduced maneuverability compared to a trapezoidal and rectangular wing

Pros:
1. Aerodynamically efficient - lower induced drag and better efficiency.
2. Excellent Glide ratio
3. Smooth Handling

# Order of best options

1. Rectangular
a. Rectangular With a slight tip at the end
2. Tapered
3. Elliptical

# Conclusion

Given our figures of merit such as mass, ease of manufacturing, drag and stability,

the rectangular wing may be a suitable choice due to its simplicity and potentially lighter weight. If minimizing drag and maximizing stability are of the highest priorities a elliptical wing could be the best choice, but it is far too complex to manufacture and has a higher mass. The tapered wing could provide us with a balanced approach of aerodynamic efficiency and stability but a higher difficulty of

manufacturing.

# References:

## https://iflyamerica.org/safety_wing_design.asp

## https://aviationforaviators.com/2022/06/11/types-of-aircrafts-wings/?expand_article

=1 (https://aviationforaviators.com/2022/06/11/types-of-aircrafts-wings/?expand_article=1)

## https://practicalaero.com/wp-content/uploads/2010/04/NASA-SP-367.pdf

## AIAA DFB 2023-2024 Rules

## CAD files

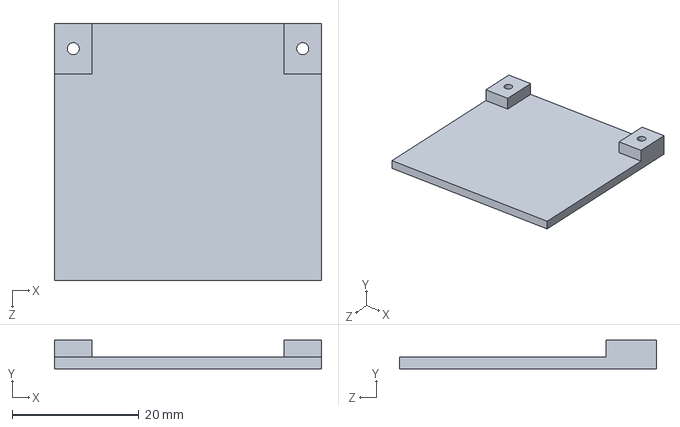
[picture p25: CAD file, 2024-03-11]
CAD/3D prints/servo bracket.SLDPRT
42.2 x 4.57 x 40.6 mm

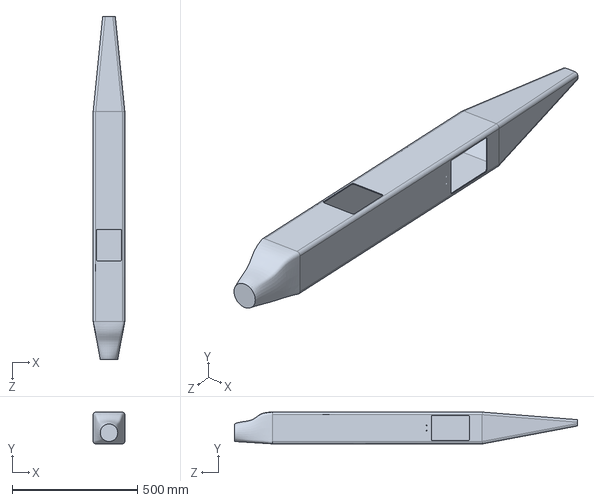
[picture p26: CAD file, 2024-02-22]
CAD/AC components/Fuselage/FuselageV1.SLDPRT
127.0 x 127.0 x 1371.6 mm

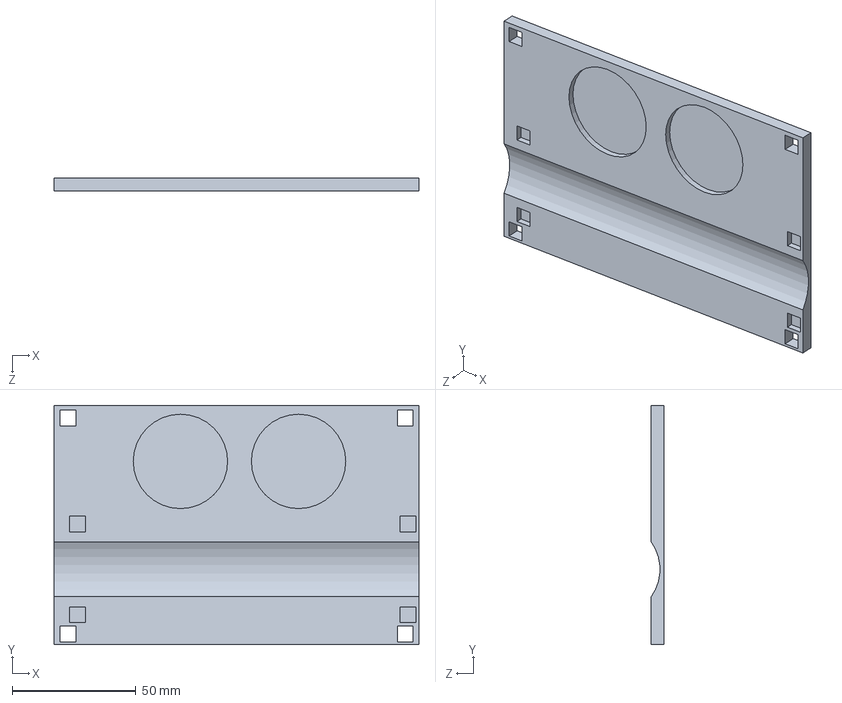
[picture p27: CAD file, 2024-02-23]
CAD/AC components/Payload/Mission 2_new/EMT_Patient_sled_top.SLDPRT
147.3 x 96.5 x 5.08 mm

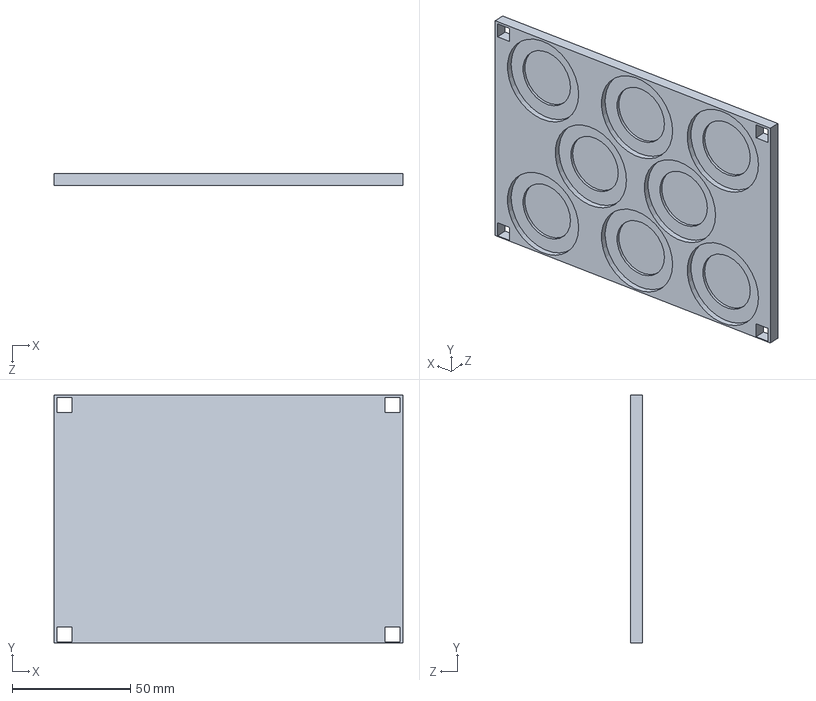
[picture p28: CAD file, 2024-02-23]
CAD/AC components/Payload/Mission_3_bottom.SLDPRT
147.3 x 104.6 x 5.08 mm

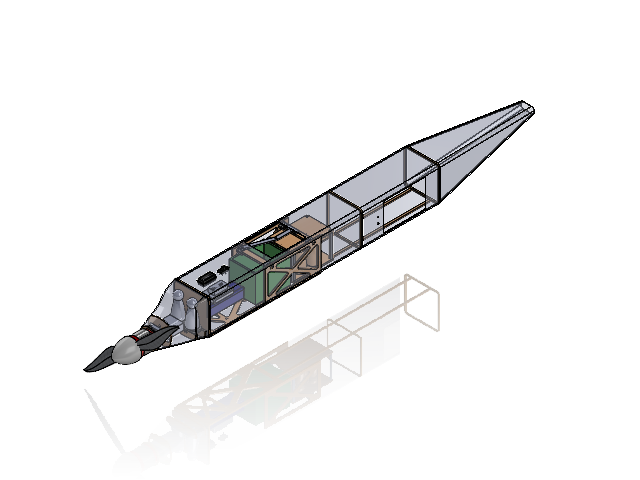
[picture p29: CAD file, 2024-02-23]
CAD/Assemblies/fuselageV1_M2.SLDASM
FuselageV1
Passenger,Crew,EMT x 2
Leopard 6354-10T
5100mAh 4s 70c battery
FrSky S6R Receiver
avionics battery
70mm prop spinner
18''_prop_ccw
PHOENIX EDGE HV 60 AMP ESC
strengthener x 3
blade fuse holder
landing_gear_plate
pilot_seats
bulkhead_real
wing_box_sides x 2
wing_mounting_prints x 4
wing_box_crossbar x 2
motor_mount_plate
motor_mount_plateV2
pilot_rib_2
pilot_rib_1
payload_struts x 2
66065K23_Slide Switch
Crew_door
stow_print
Gurney x 2
Patient
Personnel x 2
Medical_Supply_Cabinet
EMT_Patient_sled_top x 2
Mission_3_legs x 4

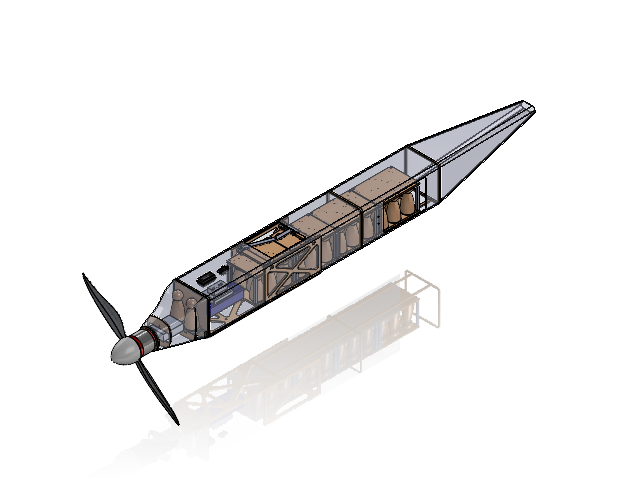
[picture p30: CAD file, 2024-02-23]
CAD/Assemblies/fuselageV1.SLDASM
FuselageV1
Passenger,Crew,EMT x 34
Leopard 6354-10T
5100mAh 4s 70c battery
FrSky S6R Receiver
avionics battery
70mm prop spinner
18''_prop_ccw
PHOENIX EDGE HV 60 AMP ESC
strengthener x 3
blade fuse holder
landing_gear_plate
Mission_3_bottom x 8
Mission_3_legs x 16
pilot_seats
bulkhead_real
wing_box_sides x 2
wing_mounting_prints x 4
wing_box_crossbar x 2
motor_mount_plate
motor_mount_plateV2
pilot_rib_2
pilot_rib_1
payload_struts x 2
66065K23_Slide Switch
Crew_door
stow_print

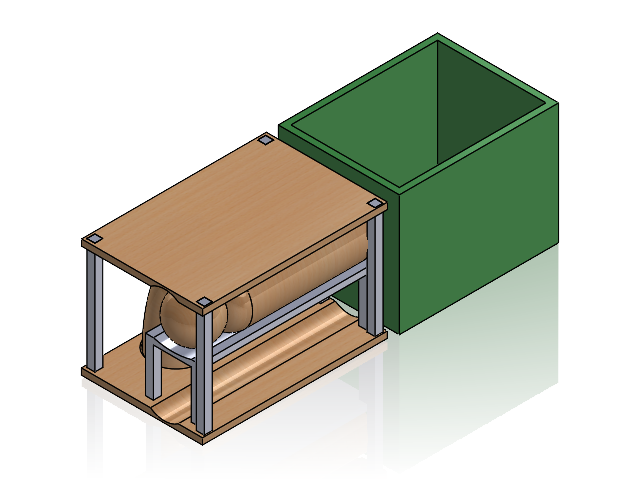
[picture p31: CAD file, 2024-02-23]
CAD/AC components/Payload/Mission 2_new/Mission_2_Assembled_new.SLDASM
Gurney x 2
Patient
Personnel x 2
Medical_Supply_Cabinet
EMT_Patient_sled_top x 2
Mission_3_legs x 4

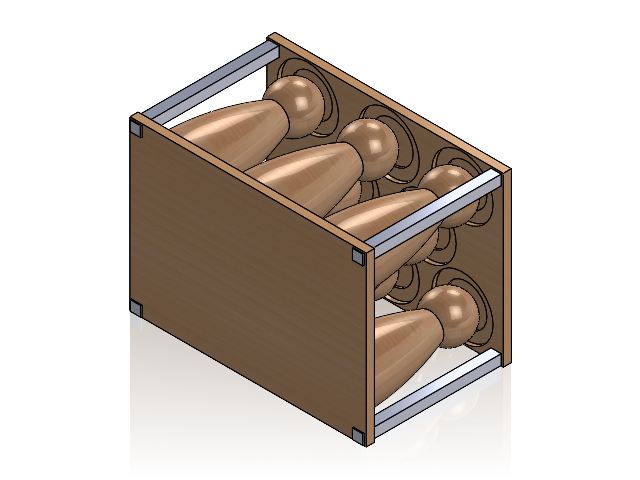
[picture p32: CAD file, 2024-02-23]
CAD/AC components/Payload/Passenger_sled_assembled.SLDASM
Mission_3_bottom x 2
Passenger,Crew,EMT x 8
Mission_3_legs x 4

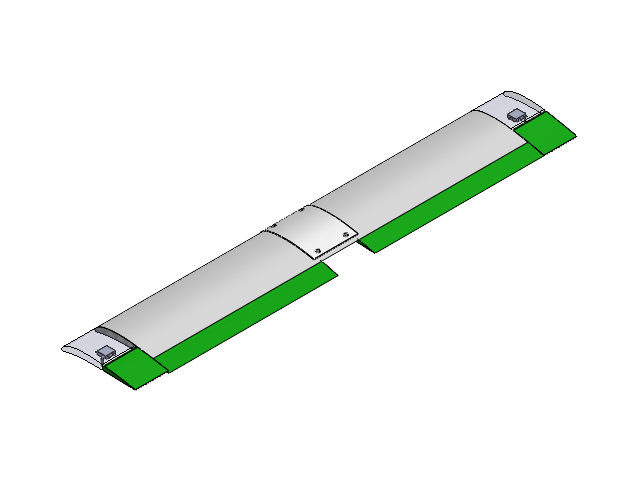
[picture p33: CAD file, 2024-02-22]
CAD/Assemblies/Mono_WingV1.SLDASM
Mono_wing_V1
GOE63_LE_aileron x 2
GOE63_TE_aileron x 2
GOE63_TE_flap_10in x 2
HS-125MG servo x 4
slim servo arm x 4
wing_mount_plate

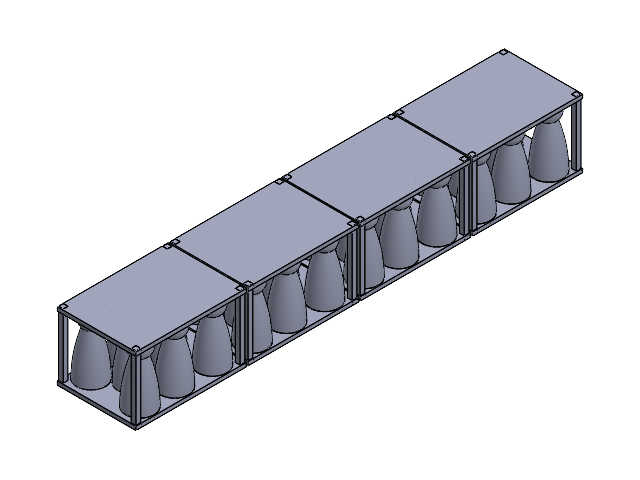
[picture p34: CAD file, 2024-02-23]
CAD/AC components/Payload/Mission_3_assembled.SLDASM
Mission_3_bottom x 8
Passenger,Crew,EMT x 32
Mission_3_legs x 16

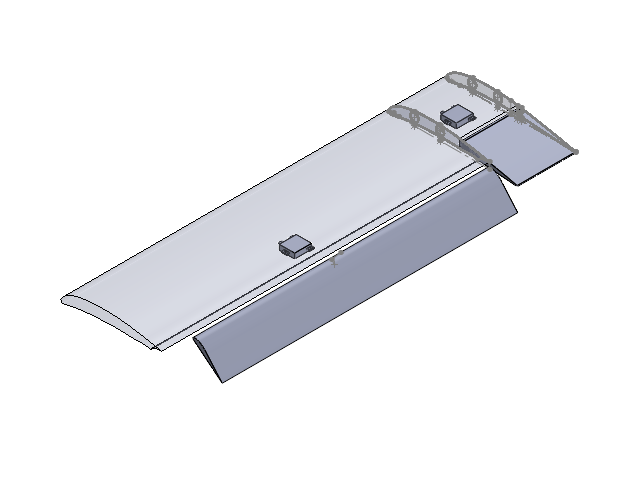
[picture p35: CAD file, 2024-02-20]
CAD/Assemblies/Right_WingV1.SLDASM
GOE63_LE_aileron
GOE63_LE_flap_10in
GOE63_TE_aileron
GOE63_TE_flap_10in
HS-125MG servo x 2

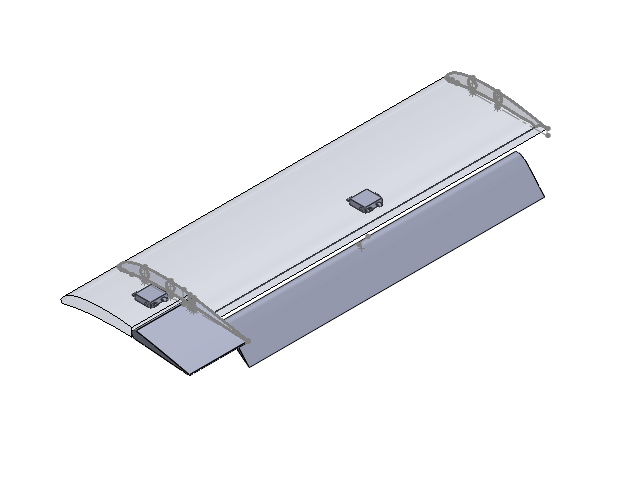
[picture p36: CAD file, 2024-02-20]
CAD/Assemblies/Left_WingV1.SLDASM
GOE63_LE_aileron
GOE63_LE_flap_10in
GOE63_TE_aileron
GOE63_TE_flap_10in
HS-125MG servo x 2

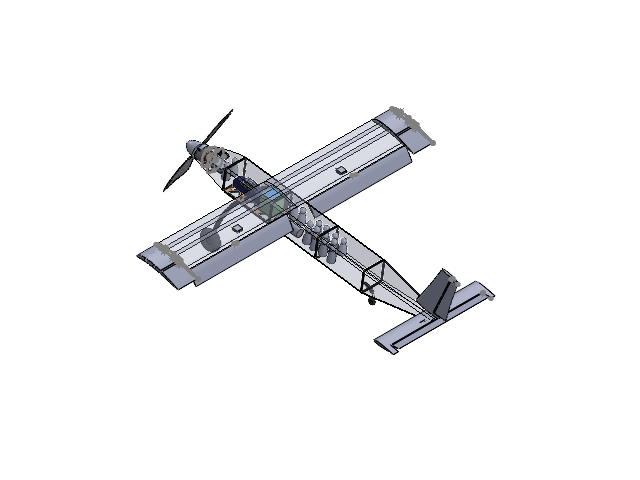
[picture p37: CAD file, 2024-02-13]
CAD/Assemblies/ToddJr_full_up.SLDASM
GOE63_LE_aileron x 2
GOE63_LE_flap_10in x 2
GOE63_TE_aileron x 2
GOE63_TE_flap_10in x 2
HS-125MG servo x 5
FuselageV1
Patient
medical supply cabinet
Passenger,Crew,EMT x 16
Leopard 6354-10T
5100mAh 4s 70c battery
FrSky S6R Receiver
avionics battery
70mm prop spinner
18''_prop_ccw
PHOENIX EDGE HV 60 AMP ESC
strengthener x 4
motor_mount_plate
Cowling vent
blade fuse holder
landing_gear_plate
motor_mount_plate_2
95868A998_Nylon Socket Head Screws x 2
90633A411_Low-Strength Steel Thin Nylon-Insert Locknut x 4
vstabV1
hstabV1
130mm_landing_gear
4.25 wheels x 2
tail wheel
92220A174_Alloy Steel Low-Profile Socket Head Screw x 2
elevatorV1
rudderV1
rear landing gear

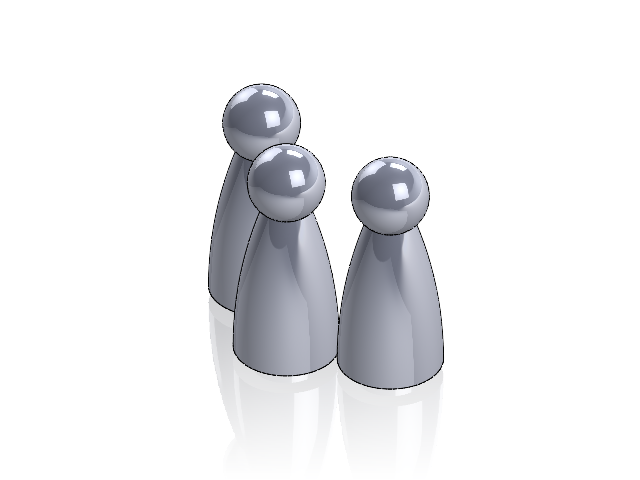
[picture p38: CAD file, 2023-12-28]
CAD/AC components/Payload/Fuselage Profile.SLDASM
Passenger,Crew,EMT x 3

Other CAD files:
CAD/Assemblies/tail_V1.SLDASM
CAD/AC components/Wings/GOE63_FULL_10in.SLDPRT
CAD/AC components/Fuselage/Mission_3_assembled.SLDASM
CAD/AC components/Fuselage/Passenger_sled_assembled.SLDASM
CAD/3D prints/Cowling vent.SLDPRT
CAD/3D prints/blade fuse holder.SLDPRT
CAD/3D prints/motor mount plate.SLDPRT
CAD/3D prints/pilot_seats.SLDPRT
CAD/3D prints/stow_print.SLDPRT
CAD/3D prints/tail print.SLDPRT
CAD/3D prints/wing_mount_plate.SLDPRT
CAD/3D prints/wing_mounting_prints.SLDPRT
CAD/AC components/Fuselage/Crew_door.SLDPRT
CAD/AC components/Fuselage/Mission_3_bottom.SLDPRT
CAD/AC components/Fuselage/Mock Fuselage.SLDPRT
CAD/AC components/Fuselage/Passenger_door.SLDPRT
CAD/AC components/Fuselage/Payload_Encasing.SLDPRT
CAD/AC components/Fuselage/bulkhead.SLDPRT
CAD/AC components/Fuselage/bulkhead_real.SLDPRT
CAD/AC components/Fuselage/landing_gear_plate.SLDPRT
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

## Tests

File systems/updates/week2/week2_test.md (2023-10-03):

summary: Week # 5 Date: 09/23/23 - 09/29/23

Aerodynamics Team

Due milestones:

-   First team meeting and divide parts for each member.

Completed milestones:

-   The first team meeting was held on 09/25/23.



Costs: $0

Upcoming milestones:

-   Make a trade matrix for each component by October 15
    
-   Finish Preliminary Model by Nov 1st

Additional Comments:

Structures Team (Wed)

Due milestones:

-   First team meeting and general schedule discussion

Completed milestones:

-   First team meeting 09//27/23 manual given to team members for machines.

Cost: $0

Upcoming milestones:

-   Learn the program for structures machines for next week's practice for laser and foam cutting.

Additional Comments:

Structures Team (Fri)

Due milestones:

-   Members attending the first meeting.
    
-   First team meeting and general schedule discussion

Completed milestones:

-   Members have been introduced to each other and assigned tasks such as wing trade studies.

Cost: $0

Upcoming milestones:

-   Members are looking to go through the Innovation Idea Labs training, analysis of wing geometry, and begin trade studies.
    
-   October 31st: First Report
    
-   November 2nd - Lockheed Martin Presentation

Additional Comments: N/A

Payload Team

Due milestones:

-   First team meeting and general schedule discussion

Completed milestones:

-   First team meeting and general schedule discussion

Cost: $0

Upcoming milestones:

-   Familiarize team members with Solidworks
    
-   Draft Top and Side Views with Dimensions and Fully Assembled
    
-   Brainstorm Latching System for Crew and Passenger Doors
    
-   Brainstorm method to secure EMT’s, Patient, and Medical Cabinet
    
-   Brainstorm  method to assemble payload into floor inserts for ground mission in 5 minutes
    
-   End of October: First Mock Up
    
-   November 15th -20th: First Physical Model
    
-   Mid-November: Propulsion Trade Studies

-   Mid-November: Test Propulsion Systems
    
-   End of January: Final Payload Assembly connect w/ Fuselage

Additional Comments: Focus on either Mission 2 or 3

Systems Team

Due milestones:

-   First team meeting, proposal format
    
-   schedule discussion,
    
-   join another sub-team meeting and join GitHub.

Completed milestones:

-   The first meeting was done on 09/25/23,
    
-   The proposal format was ready and shared,
    
-   all members joined GitHub.
    
-   Last year's comments for the proposal were read and shared.
    
-   Top 3 reports and proposals shared.

Cost: $0

Upcoming milestones:

-   Friday 09/29/23 write proposal parts 2.0 management summary, 2.3 schedules, 3.1 mission requirements, and 3.2 scoring sensitivity.
    
-   Due October 6th continue working on the proposal with new information of each sub-team.

Additional Comments:

Due October 6th continue working on the proposal with new information of each sub-team.
Additional Comments:

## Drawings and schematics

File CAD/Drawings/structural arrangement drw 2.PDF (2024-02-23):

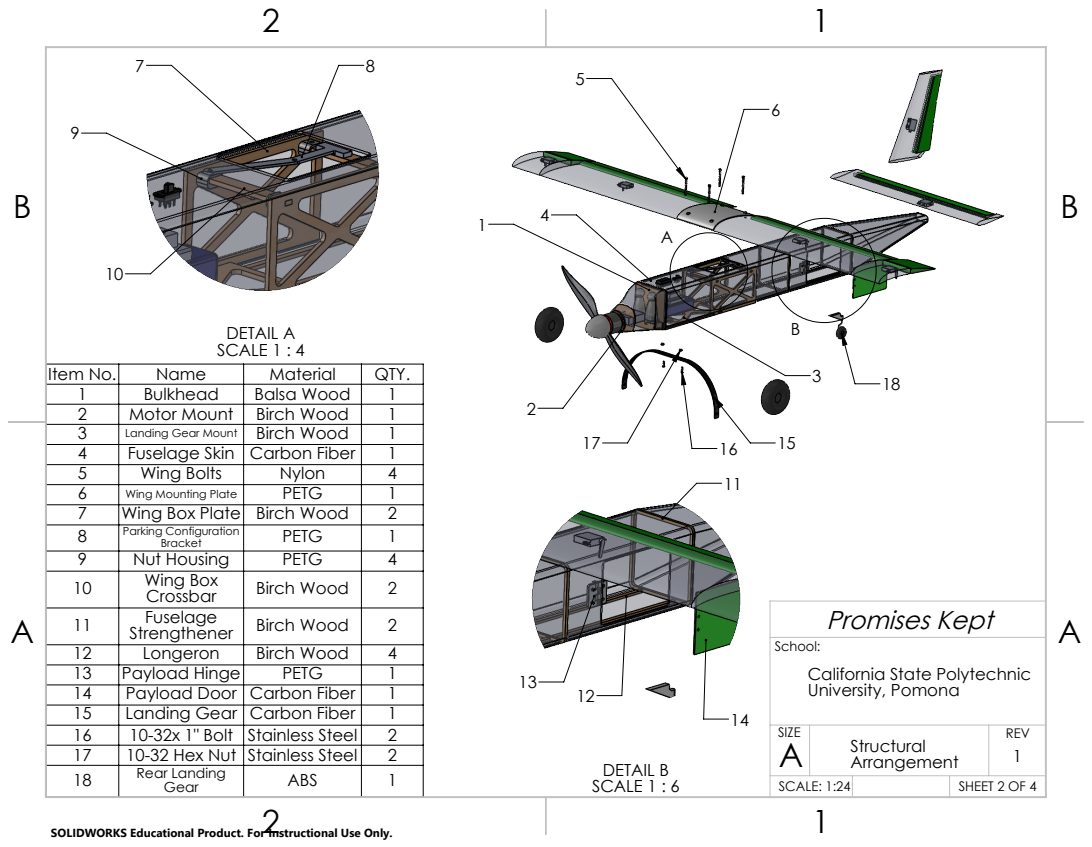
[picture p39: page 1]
DETAIL A SCALE 1 : 4; DETAIL B SCALE 1 : 6; Promises Kept; California State Polytechnic University, Pomona; 1 Structural; 10-32x 1" Bolt; Stainless Steel

Item No. | Name | Material | QTY.
1 | Bulkhead | Balsa Wood | 1
2 | Motor Mount | Birch Wood | 1
3 | Landing Gear Mount | Birch Wood | 1
4 | Fuselage Skin | Carbon Fiber | 1
5 | Wing Bolts | Nylon | 4
6 | Wing Mounting Plate | PETG | 1
7 | Wing Box Plate | Birch Wood | 2
8 | Parking Configuration Bracket | PETG | 1
9 | Nut Housing | PETG | 4
10 | Wing Box Crossbar | Birch Wood | 2
11 | Fuselage Strengthener | Birch Wood | 2
12 | Longeron | Birch Wood | 4
13 | Payload Hinge | PETG | 1
14 | Payload Door | Carbon Fiber | 1
15 | Landing Gear | Carbon Fiber | 1
17 | 10-32 Hex Nut | Stainless Steel | 2
18 | Rear Landing Gear | ABS | 1

SCALE: 1:24 | SHEET 2 OF 4

SOLIDWORKS Educational Product. For Instructional Use Only.

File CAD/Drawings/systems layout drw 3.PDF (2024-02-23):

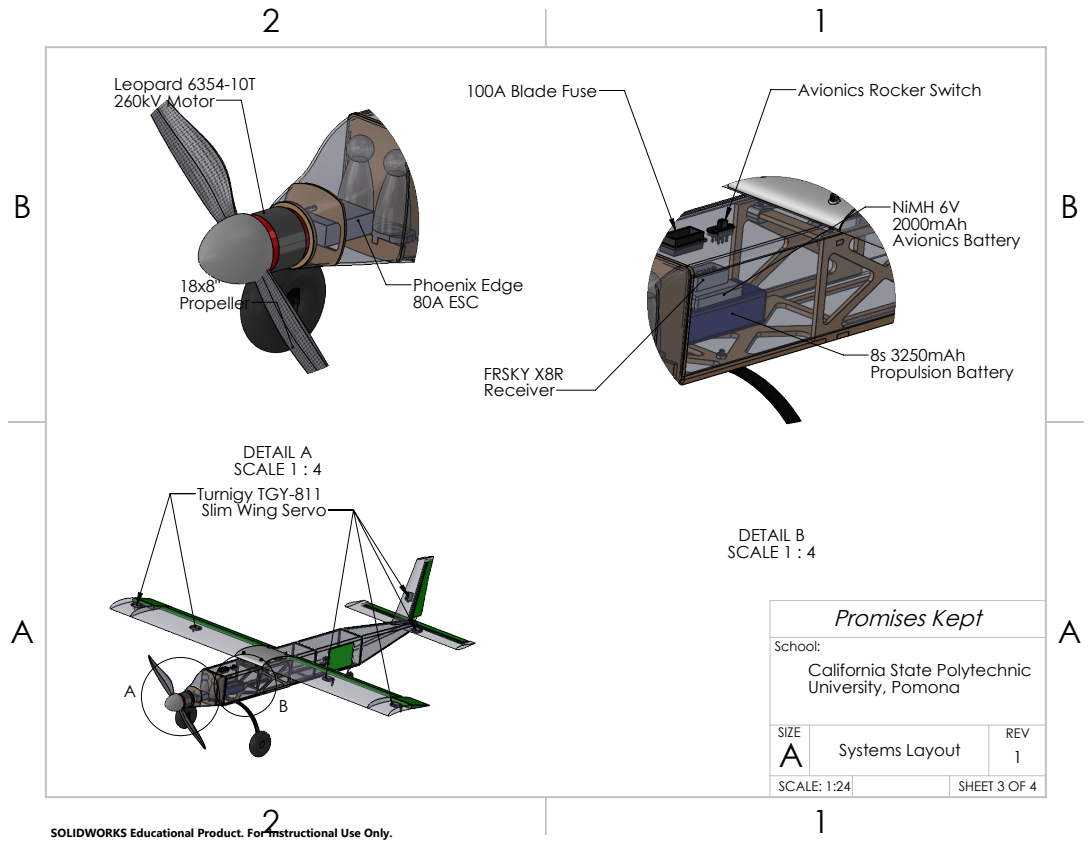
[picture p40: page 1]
Leopard 6354-10T 260kV Motor; Phoenix Edge 80A ESC; DETAIL B SCALE 1 : 4; 100A Blade Fuse; Avionics Rocker Switch; FRSKY X8R; NiMH 6V Avionics Battery; 8s 3250mAh Propulsion Battery; Promises Kept

DETAIL A
SCALE 1 : 4
Turnigy TGY-811
Slim Wing Servo

School:
California State Polytechnic
University, Pomona

SIZE A | REV 1 Systems Layout

SCALE: 1:24 | SHEET 3 OF 4

SOLIDWORKS Educational Product. For Instructional Use Only.

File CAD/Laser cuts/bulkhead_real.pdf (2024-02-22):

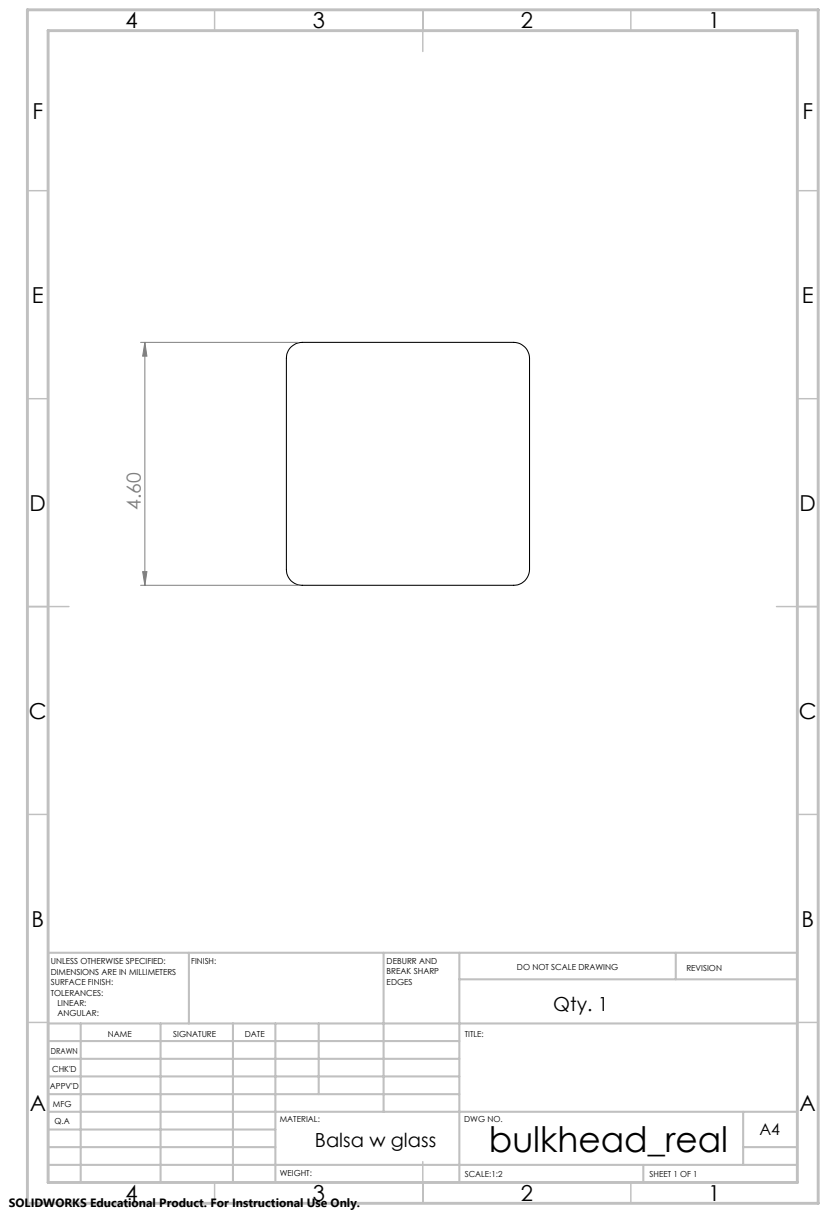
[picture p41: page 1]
Qty. 1; FINISH:; DEBURR AND; BREAK SHARP; DO NOT SCALE DRAWING; REVISION; SCALE:1:2; SHEET 1 OF 1

UNLESS OTHERWISE SPECIFIED:
DIMENSIONS ARE IN MILLIMETERS
SURFACE FINISH:
TOLERANCES:
LINEAR:
ANGULAR:

NAME | SIGNATURE | DATE | | | | TITLE:

DRAWN
CHK'D
APPV'D
MFG
Q.A | | | | MATERIAL: Balsa w glass | DWG NO. bulkhead_real | A4

SOLIDWORKS Educational Product. For Instructional Use Only.

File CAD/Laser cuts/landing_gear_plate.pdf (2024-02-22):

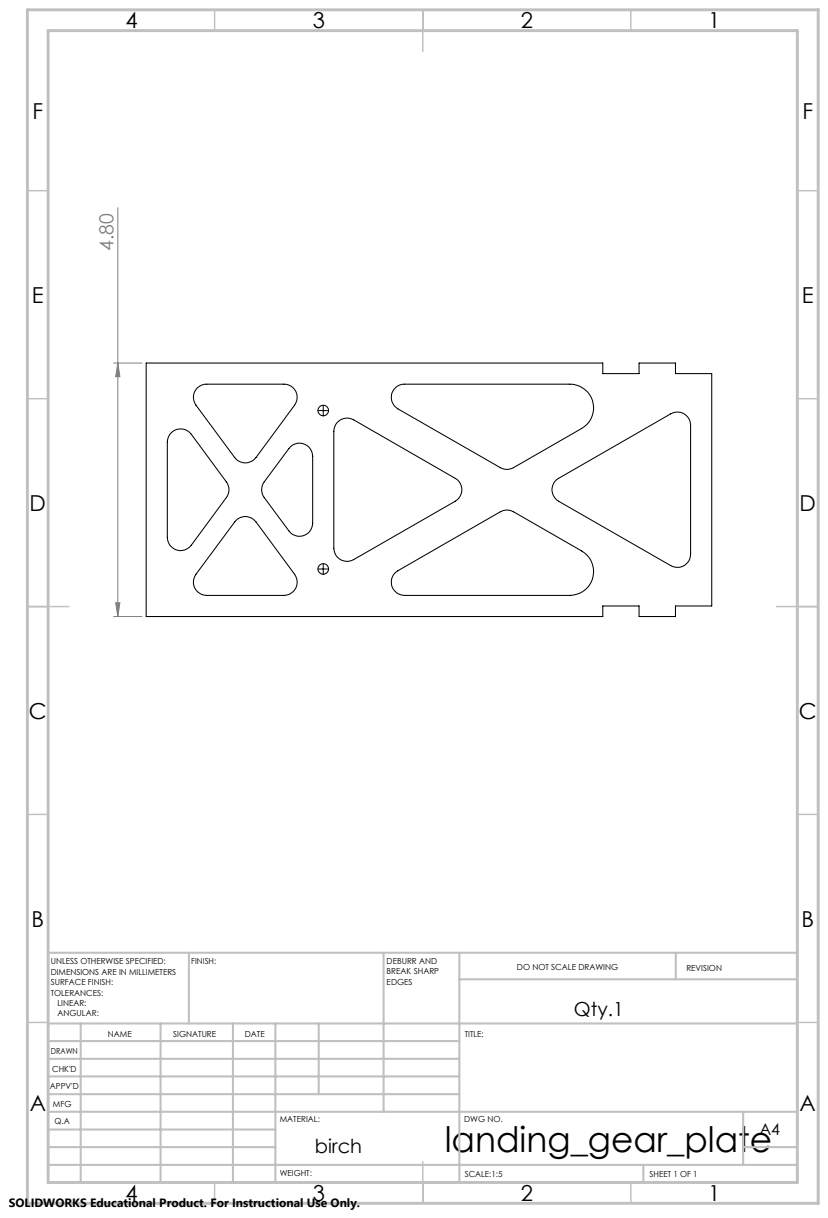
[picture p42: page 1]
FINISH:; DEBURR AND; BREAK SHARP; DO NOT SCALE DRAWING; REVISION; SCALE:1:5; SHEET 1 OF 1

UNLESS OTHERWISE SPECIFIED:
DIMENSIONS ARE IN MILLIMETERS
SURFACE FINISH:
TOLERANCES:
LINEAR:
ANGULAR:

NAME | SIGNATURE | DATE | | | | TITLE:

DRAWN
CHK'D
APPV'D
MFG
Q.A | | | | MATERIAL: landing_gear_plate birch | DWG NO. | A4

SOLIDWORKS Educational Product. For Instructional Use Only.

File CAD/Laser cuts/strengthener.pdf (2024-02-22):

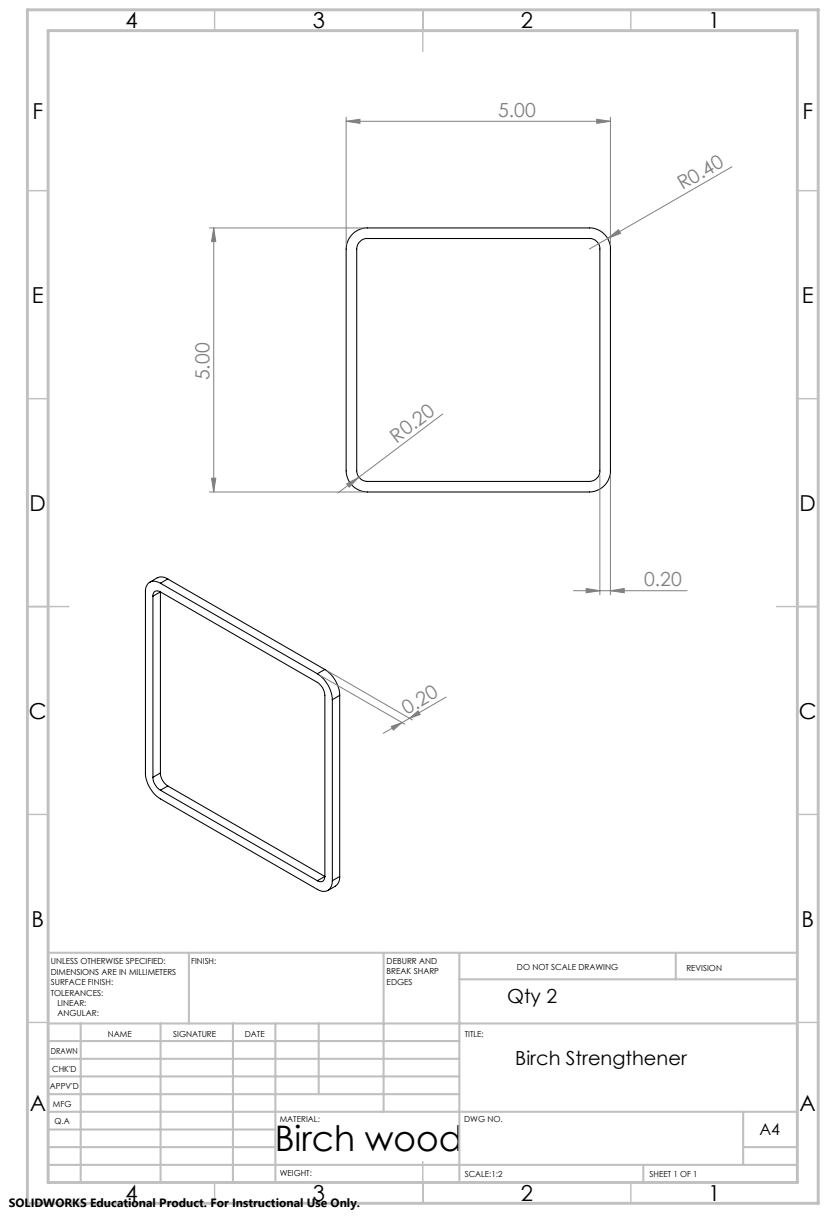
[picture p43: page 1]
Qty 2; FINISH:; DEBURR AND; BREAK SHARP; DO NOT SCALE DRAWING; REVISION; SCALE:1:2; SHEET 1 OF 1

UNLESS OTHERWISE SPECIFIED:
DIMENSIONS ARE IN MILLIMETERS
SURFACE FINISH:
TOLERANCES:
LINEAR:
ANGULAR:

NAME | SIGNATURE | DATE | | | | TITLE: Birch Strengthener

DRAWN
CHK'D
APPV'D
MFG
Q.A | | | | MATERIAL: Birch wood | DWG NO. | A4

SOLIDWORKS Educational Product. For Instructional Use Only.

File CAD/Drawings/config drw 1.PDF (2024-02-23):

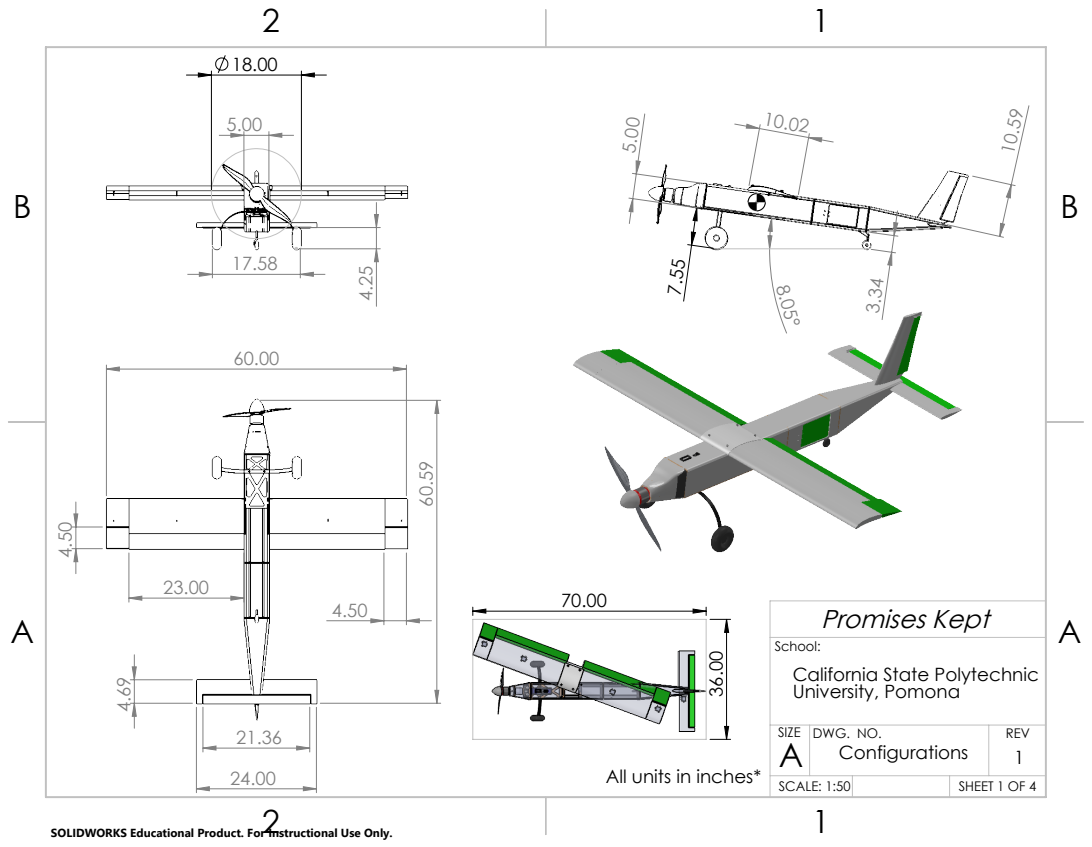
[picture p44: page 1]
Promises Kept

School:
California State Polytechnic
University, Pomona

SIZE A | DWG. NO. Configurations | REV 1

All units in inches*

SCALE: 1:50 | | SHEET 1 OF 4

SOLIDWORKS Educational Product. For Instructional Use Only.

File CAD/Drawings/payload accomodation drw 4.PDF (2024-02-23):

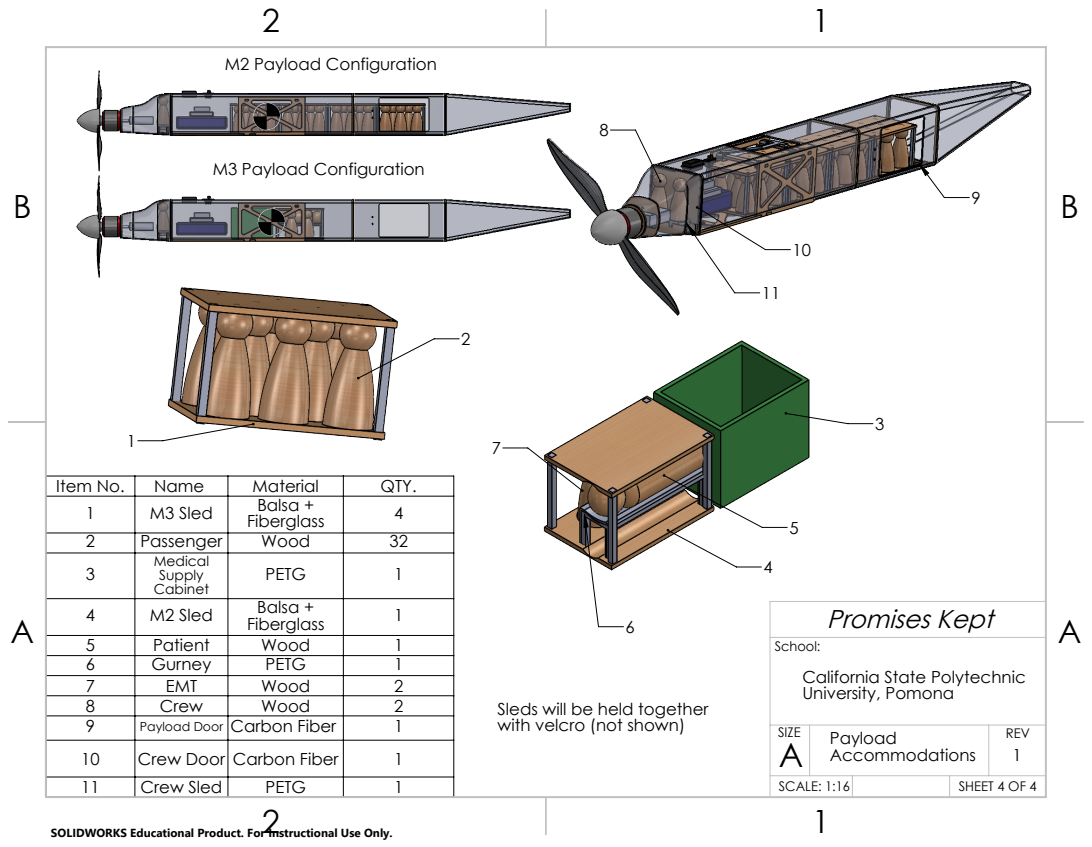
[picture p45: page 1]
M3 Payload Configuration; M2 Payload Configuration; Promises Kept; M2 Sled; Balsa +; Crew Sled; PETG; SCALE: 1:16; SHEET 4 OF 4

Item No. | Name | Material | QTY.
1 | M3 Sled | Balsa + Fiberglass | 4
2 | Passenger | Wood | 32
3 | Medical Supply Cabinet | PETG | 1

School:
California State Polytechnic
University, Pomona

6 | Gurney | PETG | 1
7 | EMT | Wood | 2
8 | Crew | Wood | 2
9 | Payload Door | Carbon Fiber | 1
10 | Crew Door | Carbon Fiber | 1

Sleds will be held together
with velcro (not shown)

SIZE A | Payload Accommodations | REV 1

SOLIDWORKS Educational Product. For Instructional Use Only.

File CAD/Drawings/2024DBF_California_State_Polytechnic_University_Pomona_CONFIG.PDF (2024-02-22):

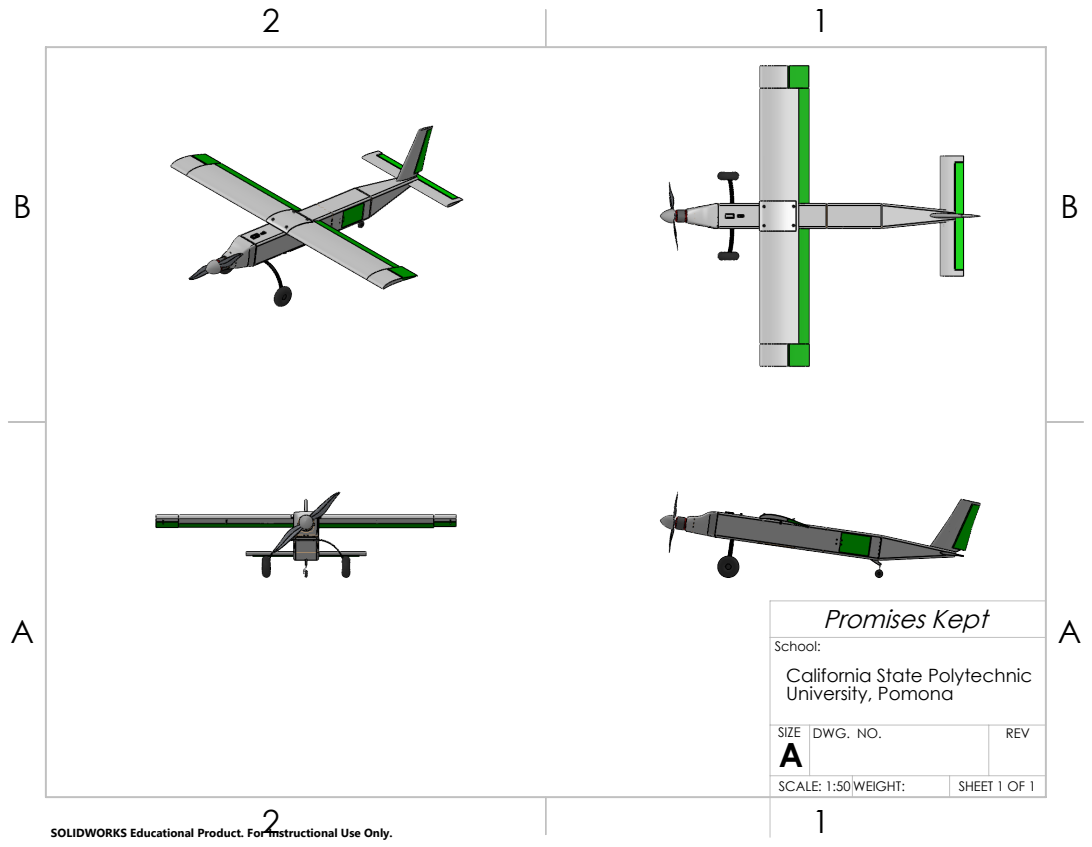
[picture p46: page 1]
Promises Kept

School:
California State Polytechnic
University, Pomona

SIZE A | DWG. NO. | REV

SCALE: 1:50 WEIGHT: | | SHEET 1 OF 1

SOLIDWORKS Educational Product. For Instructional Use Only.

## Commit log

2023-09-19 placeholders added for cad
2023-09-27 added wing weights analysis
2023-10-18 hand calc parts, initial sizing
    [Fuselage Profile.SLDASM, Fuselage sizing.SLDPRT, Mock Assembly.SLDASM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]
2023-12-22 added cots components from last year
    [5100mAh 4s 70c battery.SLDPRT, FrSky S6R Receiver.SLDPRT, HS-125MG servo.SLDPRT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]
2023-12-22 goe foil
    [GOE63_LE_10in.SLDPRT, GOE63_LE_scaled.SLDPRT]
2023-12-28 Todd Jr rough shapes
    [130mm_landing_gear.SLDPRT, 16x8 wood propeller.SLDPRT, 18''_prop_ccw.SLDPRT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]
2023-12-28 updated todd jr
    [ToddJr_full_up.SLDASM, fuselageV1.SLDASM]
2023-12-31 updated todd jr assembly
    [18''_prop_ccw.SLDPRT, 70mm prop spinner.SLDPRT, Cowling vent.SLDPRT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]
2024-01-08 1-8 updates
    [4.25 wheels.SLDPRT, Cowling vent.SLDPRT, ToddJr_full_up.SLDASM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]
2024-01-20 bolts and gear plate
    [130mm_landing_gear.SLDPRT, 90633A411_Low-Strength Steel Thin Nylon-Insert Locknut.SLDPRT, 92220A174_Alloy Steel Low-Profile Socket Head Screw.SLDPRT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]
2024-01-21 tail surfaces and xflr
    [ToddJr_full_up.SLDASM, elevatorV1.SLDPRT, fuselageV1.SLDASM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]
2024-01-28 tried to do tail
    [FuselageV1.SLDPRT, Left_WingV1.SLDASM, Leopard 6354-10T.SLDPRT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]
2024-01-30 Attempted tail design
    [FuselageV1.SLDPRT, Left_WingV1.SLDASM, Right_WingV1.SLDASM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]
2024-02-13 added internal structure and mass balance sheet
    [95868A998_Nylon Socket Head Screws.SLDPRT, FuselageV1.SLDPRT, GOE63_TE_flap_10in.SLDPRT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]
2024-02-16 fuselage bolts added
    [91221A710_Glass-Filled Nylon Socket Head Screws.SLDPRT, 95856A235_Aluminum Nylon-Insert Locknut (1).SLDPRT, FuselageV1.SLDPRT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]
2024-02-16 before fuselage concavity
    [FuselageV1.SLDPRT, fuselageV1.SLDASM, pilot_rib_1.SLDPRT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]
2024-02-17 added wing attachment
    [GOE63_LE_aileron.SLDPRT, GOE63_LE_flap_10in.SLDPRT, Left_WingV1.SLDASM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]
2024-02-19 creating new motor mounts
    [70mm prop spinner.SLDPRT, FuselageV1.SLDPRT, blade fuse holder.SLDPRT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]
2024-02-20 fixed wing mounting holes
    [FuselageV1.SLDPRT, GOE63_LE_flap_10in.SLDPRT, Left_WingV1.SLDASM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]
2024-02-20 added hatches
    [1635A101_Plastic Hinge with Holes.SLDPRT, 66065K23_Slide Switch.SLDPRT, Crew_door.SLDPRT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]
2024-02-22 hella yapping
    [FuselageV1.SLDPRT, GOE63_LE_aileron.SLDPRT, GOE63_TE_aileron.SLDPRT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]
2024-02-22 added drawings
    [66065K23_Slide Switch.SLDPRT, blade fuse holder.SLDPRT, fuselageV1.SLDASM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]
2024-02-22 added some drawings
    [fuselageV1.SLDASM]
2024-02-23 updated drawings
    [fuselageV1.SLDASM]
2024-02-23 added M2 payload
    [EMT_Patient_sled_top.SLDPRT, Medical_Supply_Cabinet.SLDPRT, Mission_2_Assembled_new.SLDASM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]
2024-02-23 added gurney
    [Gurney.SLDPRT]
2024-02-23 finished drawing package
    [EMT_Patient_sled_top.SLDPRT, Medical_Supply_Cabinet.SLDPRT, Mission_2_Assembled_new.SLDASM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]
2024-03-11 added servo mounts
    [mass balance sheet.xlsx, servo bracket.SLDPRT]
2024-03-12 hot wire cut profiles
    [fuselage profile.DXF, fuselage profile.SLDPRT, leading_edge_wires.DXF]
2024-03-13 other changes ..
    [mass balance sheet.xlsx]
